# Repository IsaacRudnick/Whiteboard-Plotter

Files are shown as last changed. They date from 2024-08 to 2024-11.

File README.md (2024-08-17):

# VectorPlotter

:pushpin: If the system is set up and you just want to have it draw something, follow [these steps](/documentation/DrawSomething.md).

TODO: Picture of system on whiteboard

## Overview

This repository has everything necessary to assemble your own robot capable of plotting of SVG files on a whiteboard (or other surface). The existing code automatically handles outlining, scaling, and positioning of any SVG file along with commanding the robot to draw the image.

## Hardware

The VectorPlotter robot is built using an Arduino to handle implementation of the abstracted commands sent by the Python script. The robot is controlled by two stepper motors, one at each upper corner of the canvas. The pen is attached to a 3D-printed pen-holder assembly which uses a servo to raise and lower the pen, allowing noncontinuous lines to be drawn.

See the [Hardware Guide](/documentation/HardwareGuide.md) for a list of all necessary components and assembly instructions.

## Software

The VectorPlotter software is split into two parts: the Arduino code and the Python code. The Arduino code is responsible for interfacing with the hardware and executing the commands sent by the Python code. The Python code is responsible for reading the SVG file, scaling and positioning it on the canvas, and sending the commands to the Arduino to draw the image.

See the [Software Setup Guide](/documentation/SoftwareSetup.md) for a list of all necessary software and setup instructions.

## Usage

See the [How to Use](/documentation/DrawSomething.md) for instructions on how to use the software once everything is set up.

## Troubleshooting

See the [Troubleshooting Guide](/documentation/Troubleshooting.md) for common issues and solutions.

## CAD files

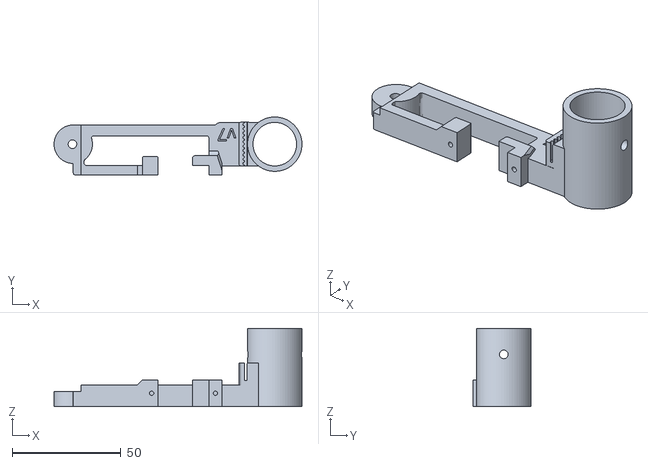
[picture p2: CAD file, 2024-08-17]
prints/VP_Pen_Holder.stl
113.9 x 26.7 x 36.0

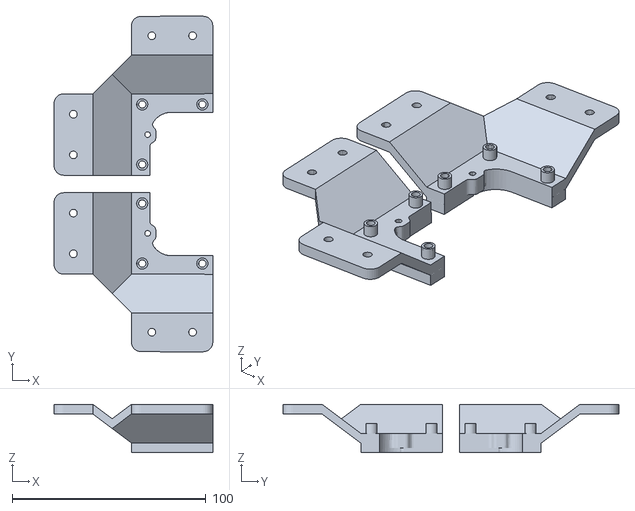
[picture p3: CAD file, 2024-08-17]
prints/VP_Bracket.stl
82.0 x 173.1 x 25.0

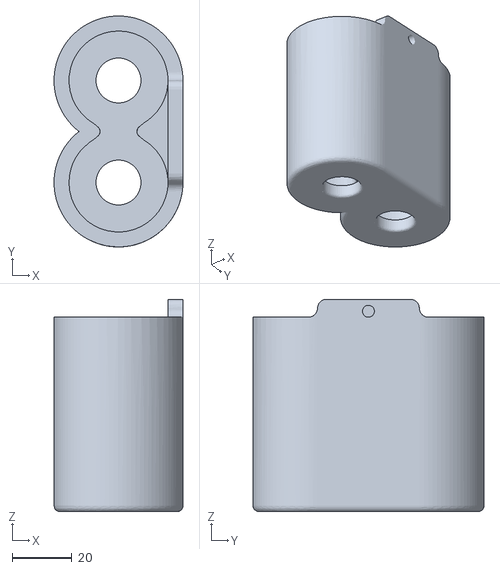
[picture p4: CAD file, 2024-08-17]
prints/VP_WeightHolder.stl
43.1 x 77.2 x 71.0

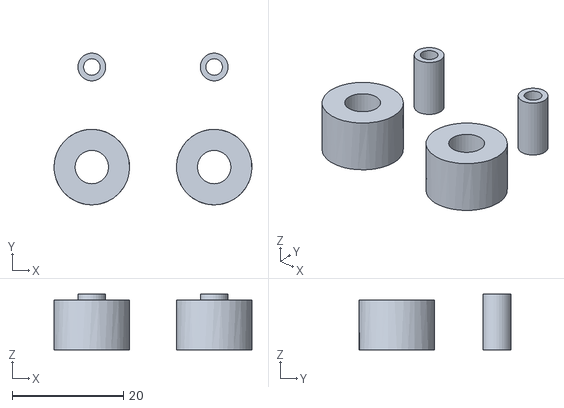
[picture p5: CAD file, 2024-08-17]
prints/VP_Sleeve_Spinner.stl
35.6 x 27.3 x 10.0

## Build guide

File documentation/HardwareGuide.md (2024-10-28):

# Hardware Requirements

## Items Needed

| Quantity | Name / Link |
| --- | --- |
| 1 | [Arduino Board](https://www.amazon.com/dp/B01EWOE0UU) with USB-B cable |
| 2 | [Stepper Motor Driver](https://www.amazon.com/dp/B075R88FMN) |
| 1 | [SG90 Micro Servo](https://www.amazon.com/dp/B07MLR1498) |
| 2 | [NEMA 17 Stepper Motors](https://www.amazon.com/dp/B0B38GHRH8) |
| 1 | [approx. 12V/1.5A DC Power Supply](https://www.amazon.com/dp/B0D2KNBHKG)  |
| 2 | [5mm Bore GT2 Pulley for 10mm Belt](https://www.amazon.com/dp/B09X18H75P) |
| 1 | [10mm 2GT Belt](https://www.amazon.com/dp/B0BYVC7K7J) |

> Note that only 2 pulleys are needed, but the link is for a pack of 5, so you only need to buy one pack.

There are also some misc. requirements which will depend on the specifics of your build. These include:

- Whiteboard, wall, etc. to plot on
- Whiteboard Marker, Sharpie, etc. to draw with
- Various Arduino Jumper Wires
- Some M3/M4 screws, washers, and nuts. [This kit](https://www.amazon.com/dp/B0CS67BLQJ) has all of the items needed:
  - 6 M3\*20 screws for attaching stepper motors to brackets
  - 2 M3\*16 screws and
  - 2 M3 washers for installing the bracket sleeve and spinner
  - 8 M4 screws for attaching brackets to whiteboard. Read note\*
  - 1 M4 screw and
  - 1 M4 nut for attaching/clamping the drawing implement to the pen holder
- 2 D-cell batteries for the weight holder. You may modify the weight holder for whatever weight you have (e.g., loose screws, nuts, etc.).
- A computer that can connect to the Arduino board. Consider a Raspberry Pi or an old laptop. It will need to stay connected for the duration of the drawing.

> \*Note: You may need to use different screws depending on the material of your whiteboard. I've found wood screws often work better than machine screws.

Finally, all prints in the [prints](/prints/) directory are required to build the robot.

| Name | Notes |
| --- | --- |
| VP_Bracket | Print with supports |
| VP_Pen_Holder | _None_ |
| VP_Sleeve_Spinner | Print with high infill and precision |
| VP_WeightHolder | _None_ |

# Hardware Setup

## Section 1: Wiring

The wiring setup is relatively simple. The following diagram shows how to connect the stepper motors, servo, and power supply to the Arduino board.
Wiring Diagram:

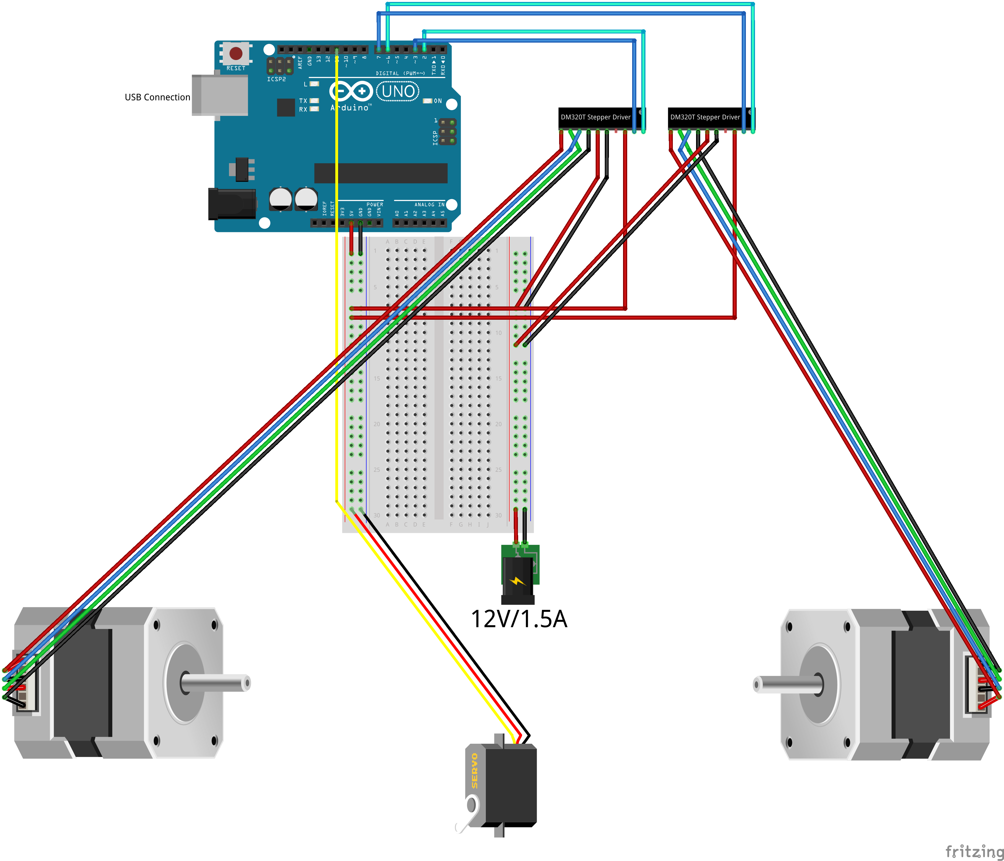
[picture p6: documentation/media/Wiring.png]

Example:

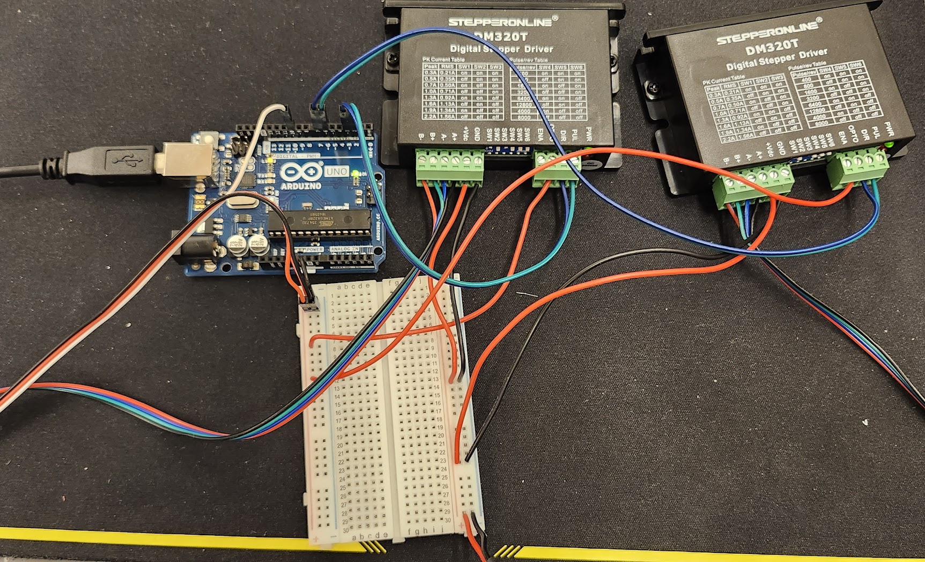
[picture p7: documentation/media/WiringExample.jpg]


## Section 2: Whiteboard

### Pen Holder Assembly

1. Install the SG90 Servo into the VP_Pen_Holder as shown below.

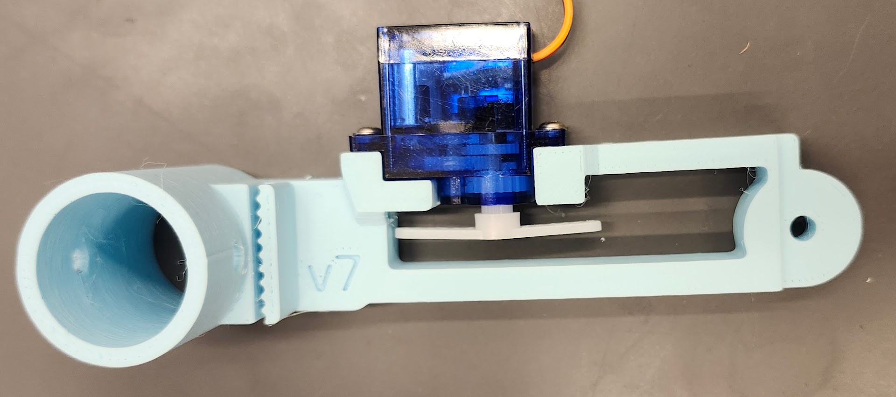
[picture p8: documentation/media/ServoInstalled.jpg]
   

1. Insert the midpoint of the belt into the VP_Pen_Holder
1. Place an M4 nut inside of the VP_Pen_Holder on the side closer to the servo.
1. Screw the M4 screw above the belt, through the VP_Pen_Holder, into the nut.

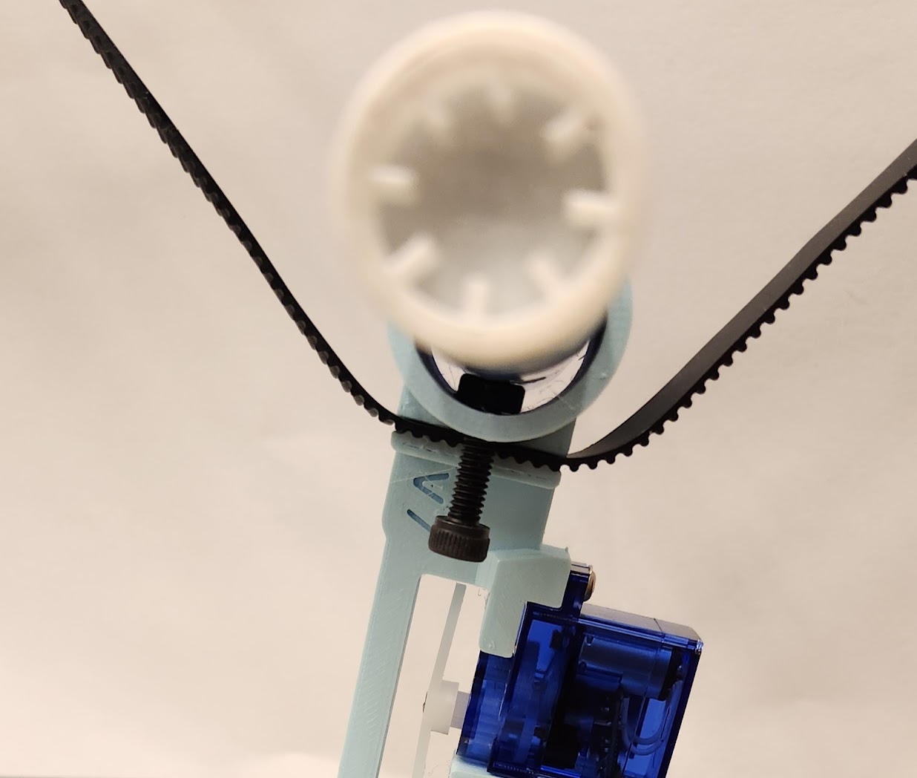
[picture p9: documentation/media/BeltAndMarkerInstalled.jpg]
   

1. Place two D-cell batteries into the VP_WeightHolder.
1. Screw an M4 screw through the VP_Pen_Holder and the VP_WeightHolder. The two should be firmly attached with no pivoting about the screw. Ensure the VP_WeightHolder is pressed flush against the VP_Pen_Holder.

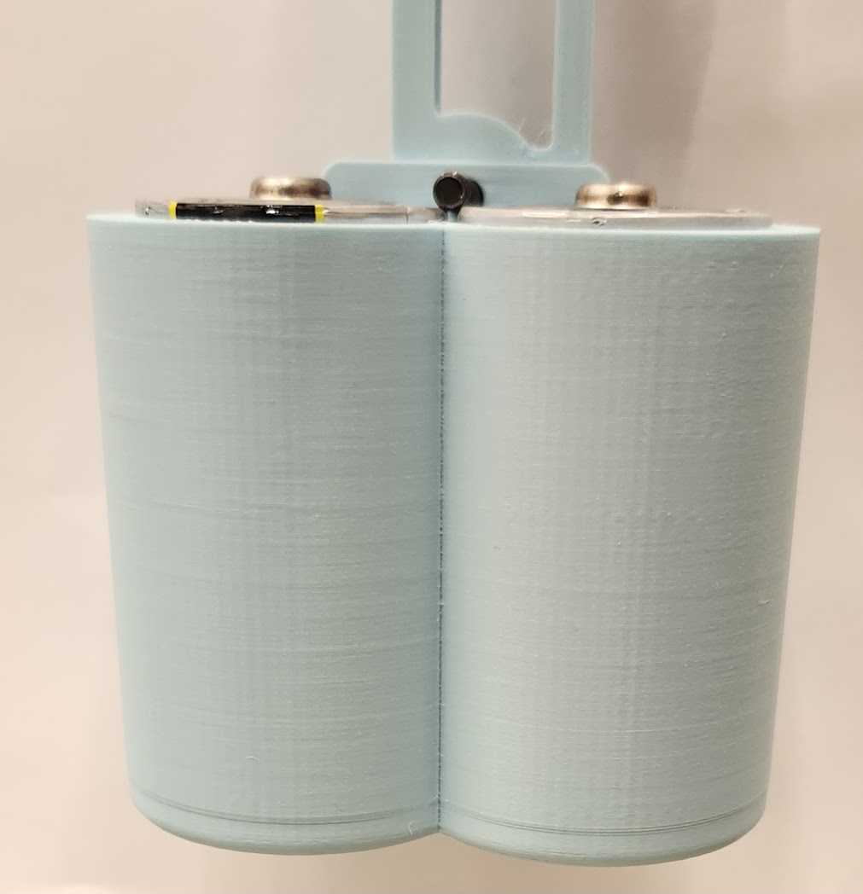
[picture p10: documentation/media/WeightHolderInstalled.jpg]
   

### Bracket Assembly

These steps will be repeated for both the left and right brackets. The pictures shown are for the right bracket, but the left bracket is a mirror image.

1. Screw an M3\*16 screw into one of the VP_Sleeve_Spinner print's smaller tubes (the "sleeve"). Place an M3 washer on the screw before screwing it in.
1. Insert the sleeve/washer/screw assembly into the larger VP_Sleeve_Spinner tube (the "spinner"). In this guide, for visibility,

- the sleeve is orange,
- the spinner is light blue, and
- the bracket is dark blue.

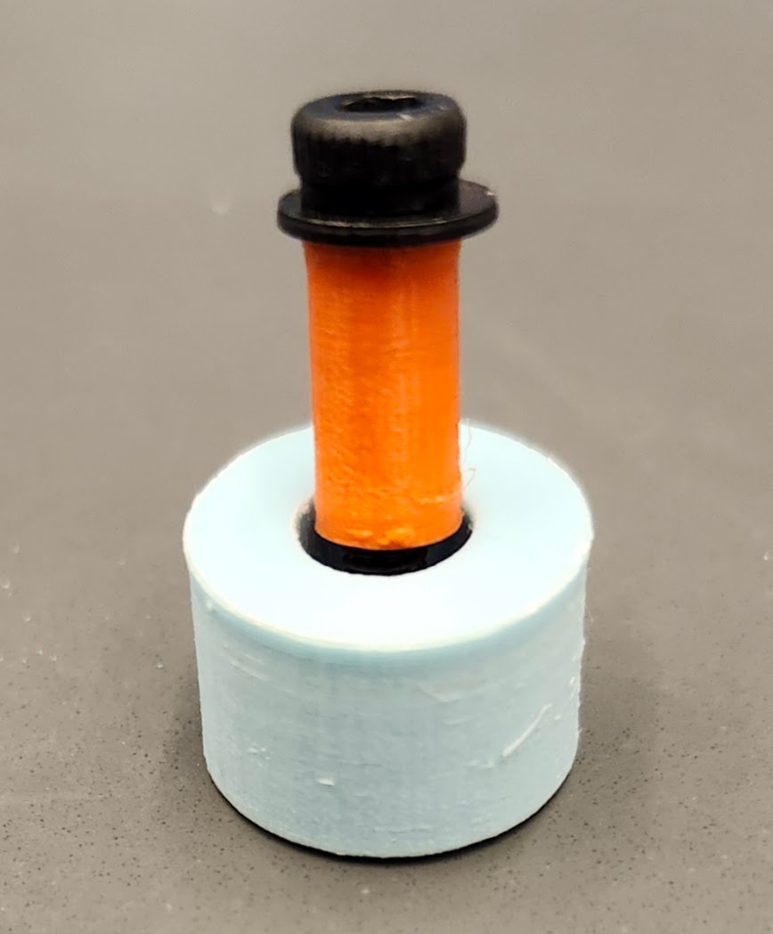
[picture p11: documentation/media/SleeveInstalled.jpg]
  

1. Screw the sleeve assembly (with the spinner around it) into the bracket as shown below.

   > The spinner should be loose and freely spin. It is ok if it wiggles when shaken.

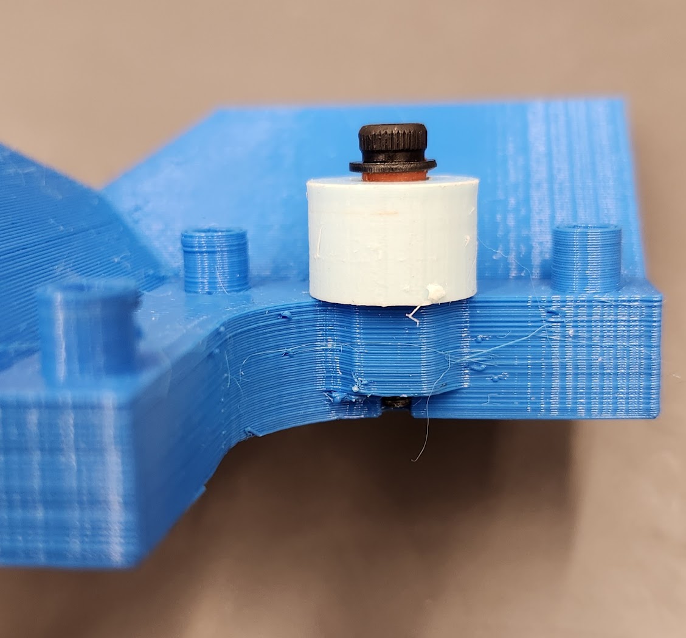
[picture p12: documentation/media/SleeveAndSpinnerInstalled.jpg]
   

1. Attach a pulleys to the stepper motor, ensuring the flat edge of the stepper motor shaft has a set screw pressing against it, as shown in the below example. Firmly tighten the set screws.

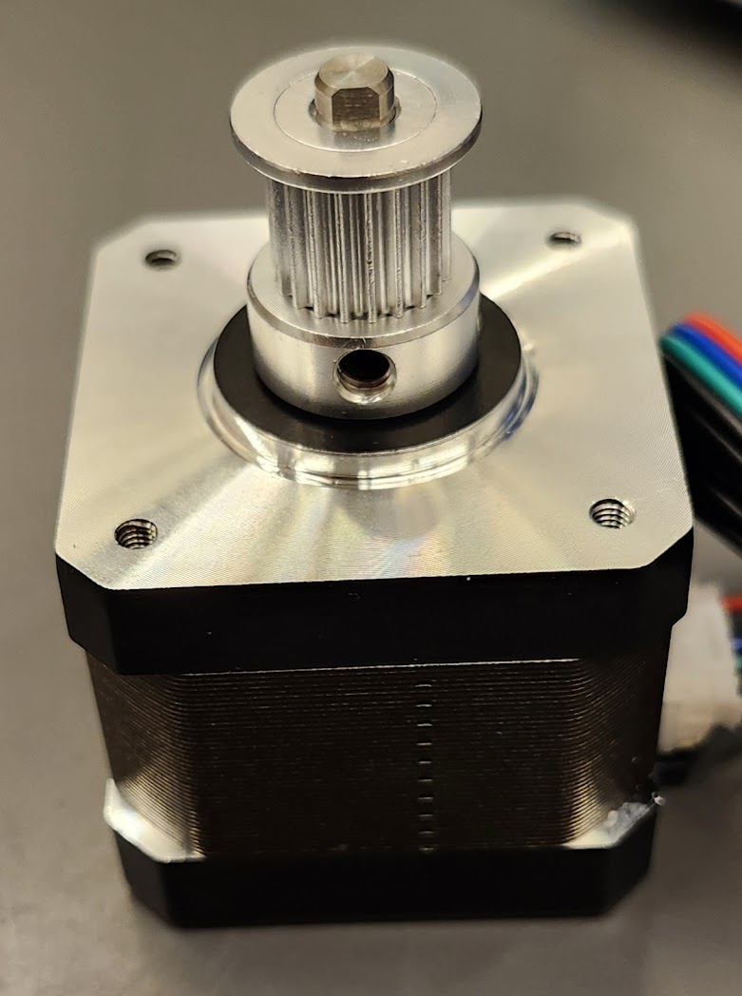
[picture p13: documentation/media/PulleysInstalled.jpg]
   

1. Attach the stepper motor to the VP_Bracket using M3\*20 screws. It is recommended to attach the stepper motor such that the wires are on one of the sides that will be facing away from the whiteboard. In the below image, those are the sides facing away from the camera.

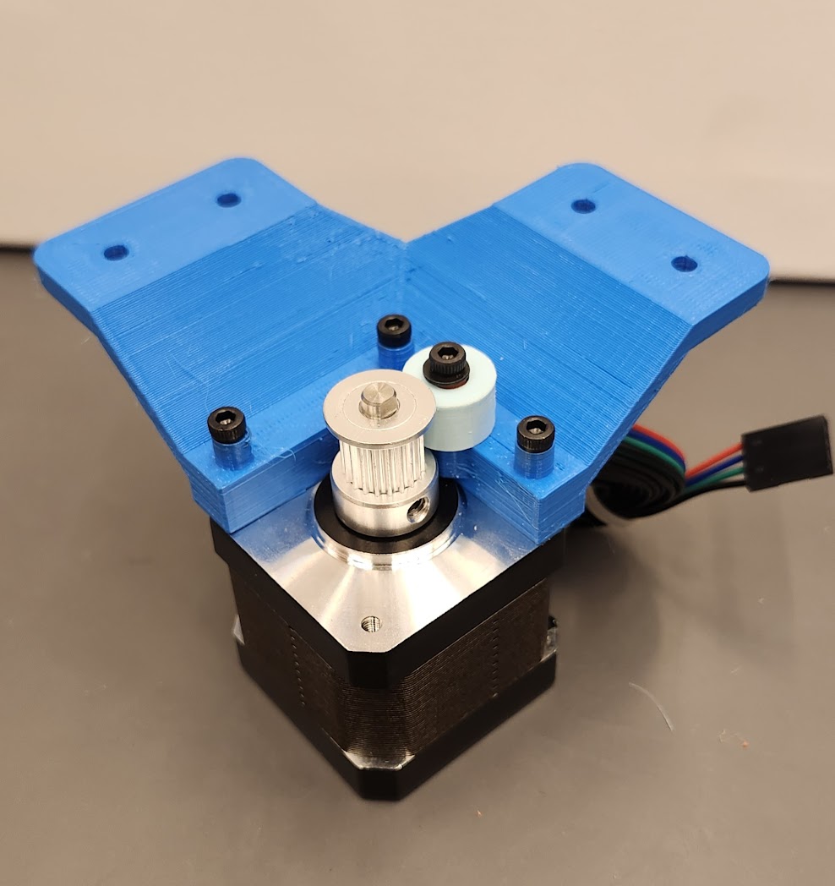
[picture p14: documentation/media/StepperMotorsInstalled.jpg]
   

1. By hand, rotate the belt into the pulley. Depower the steppers to facilitate this.
1. Attach the VP_Bracket to the whiteboard using M4 screws. On each bracket, the sleeve/spinner side should be the highest when installed (this is how to differentiate the left vs. right bracket).
   > It is recommended to drill holes in the whiteboard before screwing in the screws. You can use the bracket as a location template. Pre-drilling will help prevent the whiteboard from cracking.

This is what the top right corner of the whiteboard should look like when everything is installed (stepper wires not shown):

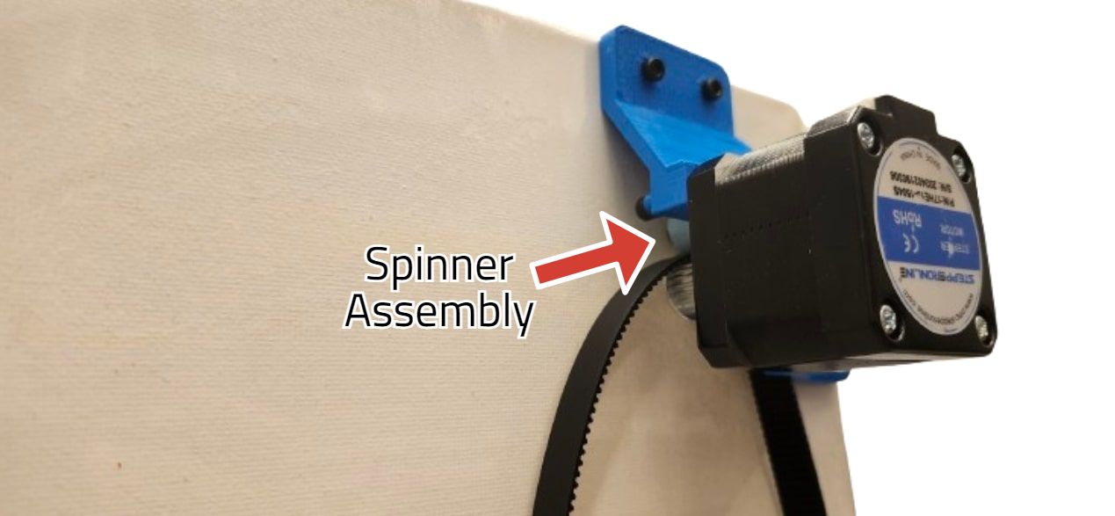
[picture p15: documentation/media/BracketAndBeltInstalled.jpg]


> Note the location of the spinner assembly, which is pointed at with a red arrow; it should be on the TOP of the belt, not to the side.

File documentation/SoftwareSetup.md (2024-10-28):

# Software Setup

This guide will walk you through the initial setup of the software, including dependencies and configuration.

## Install Dependencies

### PlatformIO

This project uses PlatformIO to manage dependencies and compile the code for the arduino. To install PlatformIO, follow the instructions on the [PlatformIO website](https://platformio.org/install/cli). You only need to upload the code to the Arduino once, so you can uninstall PlatformIO after the initial setup if you wish.

The PlatformIO project is located in the [arduino](/arduino/) directory. To upload the code to the Arduino,

1. Connect the Arduino to your computer via USB.
1. Install the PlatformIO extension in VSCode.
1. Open VSCode in the [arduino](/arduino/) directory.
1. Press `Ctrl+Alt+U` to upload the code to the Arduino.

Take note of the output from the upload process. If uploaded successfully, there should be a section that looks like this:

```
Looking for upload port...
Auto-detected: COM13
```

The port (COM13) will be used later.

### Python Setup

This project was tested with and works with Python 3.11.9. Other versions _should_ work but are untested.

Install all dependencies by running the following command in the root directory of the project:

```bash
pip install -r requirements.txt
```

## Set User Constants

The software has two constants files. The first is [constants.py](/constants.py), which contains the predefined constants for the software. The second is [user_setup.py](/user_setup.py), which you will need to set up.

`INPUT_IMG_FILE_PATH` - You will change this every time you want to draw a new image. This is the path to the SVG file you want to draw. The SVG file should be in the `user/SVGs/` directory, but this is not necessary.

`START_FROM_POINT` - This variable will be used if you want to draw a subset of an SVG. If, for some reason, the previous drawing was interrupted, you can set this variable to the point you want to start from. The default value is 0, which means the drawing will start from the beginning of the SVG. To see the point the last drawing was interrupted at, check the progress.txt file.

`MAX_CM_BETWEEN_POINTS` - used when interpolating points. Higher values will result in fewer points and faster drawing, but the drawing will be less accurate. Lower values will result in more points and slower drawing, but the drawing will be more accurate. The recommended value range is (0, 2]

`ARDUINO_USB_PORT` - The port that the Arduino is connected to. This is the port that was outputted when the code was uploaded to the Arduino. On Windows, it will look something like `COM13`. On Linux, it will look something like `/dev/ttyACM0`. If you want to find this port without uploading the arduino again, you can run the [lisb_usb_ports.py](/list_usb_ports.py) file. The port connected to the arduino will likely have "Serial" or "Arduino" in its name.

`SHOW_PREVIEW` - Whether or not to show a preview on the screen before drawing the SVG. Useful for confirming that the SVG is being placed and scaled correctly.

`TURTLE_PENSIZE` - the width of the pen in pixels. Only affects preview, not actual drawing.

`BACKGROUND_IMG_FILE_PATH` - The path to the image file that will be used as the background. This is optional. If you don't want a background image, set this to `None`.

More about the below values can be found in the [Canvas Explained](#canvas-explained) section.
`CANVAS_WIDTH` - The width in cm of the canvas.  
`CANVAS_HEIGHT` - The height in cm of the canvas.
`TOP_PADDING` - The distance in cm between the top of the canvas and the drawable area.
`LEFT_PADDING` - The distance in cm between the left side of the canvas and the drawable area.
`RIGHT_PADDING` - The distance in cm between the right side of the canvas and the drawable area.
`BOTTOM_PADDING` - The distance in cm between the bottom of the canvas and the drawable area.

### Canvas Explained

The "canvas" is a rectangular area defined by the distance between the stepper motor shafts and the distance from the stepper motor's shaft to the bottom of the board. The "frame" is the user-defined area within the canvas where the user permits the pen to draw.

The following term

| Term | Definition |
| --- | --- |
| Canvas Width | The distance in cm between the center of each stepper |
| Canvas Height  | The distance in cm between the center of the stepper and the bottom of the board |
| Frame | The drawable rectangular subarea of the canvas. Defined by the padding |
| Left Padding | The user-defined distance between the left side of the canvas and the drtawable area |
| Right Padding  | The user-defined distance between the right side of the canvas and the drawable area |
| Top Padding | The user-defined distance between the top of the canvas and the drawable area |
| Bottom Padding | The user-defined distance between the bottom of the canvas and the drawable area |

The below image illustrates these terms. In this image, the white rectangle represents the frame, which is the only area where the pen is allowed to draw.
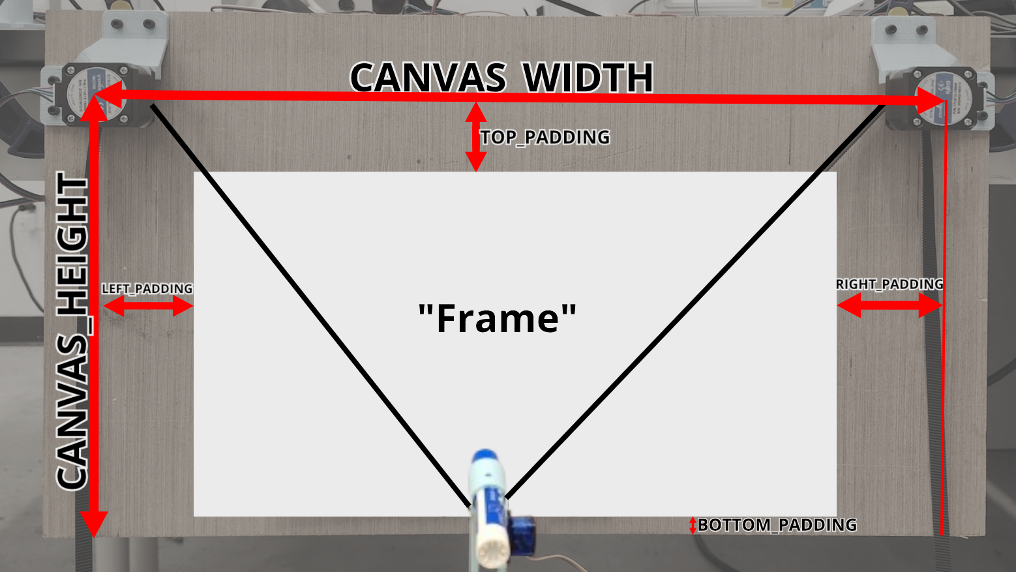
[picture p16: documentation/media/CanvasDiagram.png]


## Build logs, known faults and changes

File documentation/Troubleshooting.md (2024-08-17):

# Troubleshooting

## Table of Contents

## My motors or servo are not moving

## My motors are moving in the wrong direction

## My pen is not lifting or lowering properly

## The image curves upwards or downwards

## The image/preview don't look like my input SVG

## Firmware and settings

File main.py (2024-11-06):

from dataclasses import dataclass
from math import sqrt
import os
import time
from svgoutline import svg_to_outlines
import turtle
import constants
import user_setup as user_settings
import xml.etree.ElementTree as ET
from progress.bar import ChargingBar
import cv2
import pycomponents.ArduinoInterface as ArduinoInterface
from pycomponents.Stepper import StepperDirection as StepperDirection
from pycomponents.Servo import ServoConnectionType, ServoActuationType, ServoInverted 

# =========================================== WARNINGS =========================================== #
# Make sure user isn't accidentally starting from a point other than 0
if user_settings.START_FROM_POINT > 0:
    warning = f"NOTE: Starting from point {user_settings.START_FROM_POINT}. Press Enter to continue."
    input(warning)

# Minimum recommended padding values
min_lp = 5
min_rp = 5
min_tp = 10
min_bp = 5

# Check the padding values and warn the user if they are below the recommended minimums
lp_warning = user_settings.LEFT_PADDING < min_lp
rp_warning = user_settings.RIGHT_PADDING < min_rp
tp_warning = user_settings.TOP_PADDING < min_tp
bp_warning = user_settings.BOTTOM_PADDING < min_bp

if lp_warning or rp_warning or tp_warning or bp_warning:
    print(
        f"WARNING: Padding values are " +
        f"left: {user_settings.LEFT_PADDING}, " +
        f"right: {user_settings.RIGHT_PADDING}, " +
        f"top: {user_settings.TOP_PADDING}, " +
        f"bottom: {user_settings.BOTTOM_PADDING}.\n " +
        "Recommended minimum values are " +
        f"{min_lp}, {min_rp}, {min_tp}, {min_bp}. "
        "Make sure the pen holder fits within the canvas.")
    input("Press Enter to acknowledge.")

# ===================================== Classes and Instances ==================================== #

# Create the steppers and servo that control the physical plotter
TopLeftStepper =  ArduinoInterface.Stepper(0, StepperDirection.NORMAL)
TopRightStepper = ArduinoInterface.Stepper(1, StepperDirection.INVERTED)
MarkerToggleServo = ArduinoInterface.Servo(0,
                                           ServoConnectionType.PWM,
                                           ServoActuationType.POSITION,
                                           (500, 1500),
                                           (0, 180),
                                           ServoInverted.NORMAL)
SteppersFinishedSensor = ArduinoInterface.Sensor(0)
Arduino = ArduinoInterface.Arduino(user_settings.ARDUINO_USB_PORT,
                                   [MarkerToggleServo],
                                   [TopLeftStepper, TopRightStepper],
                                   [SteppersFinishedSensor])


@dataclass
class PointInstruction:
    """Represents a point in the drawing with instructions for the motors and pen.
    x_cm and y_cm are the coordinates of the point in cm, where the bottom left of the canvas is (0,0).
    motor_left_position and motor_right_position are the number of steps each motor needs to take to reach that point.
    pen_down_after is a boolean value that determines whether the pen should be down after reaching that point.
    """
    x_cm: float
    y_cm: float
    # Map the x and y cm to the position of each motor (in steps) to reach that point.
    # Note, steps are relative to start, not current position.
    motor_left_position: int
    motor_right_position: int
    # Put the pen down after this point or not
    pen_down_after: bool


class PenController:
    def __init__(self, ArdI: ArduinoInterface.Arduino):
        self.ArdI = ArdI

        self.pen_down = True  # Initial pen state
        self.prev_instruction = None

    def raise_pen(self):
        if self.pen_down:
            self.ArdI.set_servo(MarkerToggleServo, constants.PEN_UP_SERVO_ANGLE)
            # Wait for the steppers to finish moving before continuing
            time.sleep(0.5)
            self.pen_down = False

    def lower_pen(self):
        if not self.pen_down:
            self.ArdI.set_servo(MarkerToggleServo, constants.PEN_DOWN_SERVO_ANGLE)
            # Wait for the steppers to finish moving before continuing
            time.sleep(0.5)
            self.pen_down = True
            
    def done_moving(self):
        return self.ArdI.poll_sensor(SteppersFinishedSensor)

    def follow_instruction(self, instruction: PointInstruction):
        # Move the motors to the correct position
        self.ArdI.set_stepper(TopLeftStepper, instruction.motor_left_position)
        self.ArdI.set_stepper(TopRightStepper, instruction.motor_right_position)

        # Wait for the steppers to finish moving before continuing
        while not self.done_moving():
            print("Debug: Waiting for steppers to finish moving.")
            time.sleep(0.1)

        if instruction.pen_down_after:
            self.lower_pen()
        else:
            self.raise_pen()

        # Update the previous instruction
        self.prev_instruction = instruction


# This is how we will control moving the pen across the board and raising/lowering it (on/off the surface)
Pen = PenController(Arduino)

# ======================================= PRIMARY FUNCTIONS ====================================== #


def add_strokes_to_svg(input_file: str, output_file: str):
    """Add stroke and stroke-width attributes to all elements in an SVG file.
    This is necessary for the svgoutline library to work properly.

    Args:
        input_file (str): The path to the input SVG file.
        output_file (str): The path to the output SVG file.
    """
    # Parse the SVG file
    tree = ET.parse(input_file)
    root = tree.getroot()

    # Iterate over all elements in the SVG
    for elem in root.iter():
        # Add stroke and stroke-width attributes to each element
        # The color and width are arbitrary as far as this program is concerned. All that matters is that they are there.
        elem.set('stroke', 'red')
        elem.set('stroke-width', '2')

    # Write the updated SVG to a new file
    tree.write(output_file)


def svg_to_instructions(svg_path: str):
    """Generate a list of PointInstructions from an SVG file.

    Args:
        svg_path (str): The path to the SVG file that will be converted to instructions.
    """

    # ====================================== GET STARTING POINTS ===================================== #

    frame_width = user_settings.CANVAS_WIDTH - user_settings.LEFT_PADDING - user_settings.RIGHT_PADDING
    frame_height = user_settings.CANVAS_HEIGHT - user_settings.TOP_PADDING - user_settings.BOTTOM_PADDING

    # Get raw points. These will later be scaled to the canvas size, but may have any range of values right now.
    tree = ET.parse(svg_path)
    root = tree.getroot()
    outlines = svg_to_outlines(root)
    # List of lists of points. Each sublist is a disconnected section of the drawing.
    raw_sections = [line[2] for line in outlines]

    raw_all_points = [point for section in raw_sections for point in section]

    # Determine the minimum and maximum x and y values of the drawing
    # These will be used to scale the drawing to the canvas size
    min_x = min([point[0] for point in raw_all_points])
    max_x = max([point[0] for point in raw_all_points])
    min_y = min([point[1] for point in raw_all_points])
    max_y = max([point[1] for point in raw_all_points])

    # ============================================ SCALING =========================================== #
    # Scale all points to fit in the frame

    # Calculate the scale factor to fit the drawing to the canvas
    x_scale_factor = frame_width / (max_x - min_x)
    y_scale_factor = frame_height / (max_y - min_y)

    # Maintain aspect ratio by using the smaller scale factor
    scale_factor = min(x_scale_factor, y_scale_factor)

    # Calculate the center offset to keep the drawing centered
    x_center_offset = (frame_width - (max_x - min_x) * scale_factor) / 2
    y_center_offset = (frame_height - (max_y - min_y) * scale_factor) / 2

    def scale_raw_xy(x, y):
        """Take in a raw x and y value and scale it to the canvas size. Only used in svg_to_instructions."""
        scaled_x = (x - min_x) * scale_factor + user_settings.LEFT_PADDING + x_center_offset
        scaled_y = (y - min_y) * scale_factor + y_center_offset
        scaled_y = user_settings.CANVAS_HEIGHT - user_settings.TOP_PADDING - scaled_y
        return scaled_x, scaled_y

    sections = []

    for raw_section in raw_sections:
        section = [scale_raw_xy(x, y) for x, y in raw_section]
        sections.append(section)

    # ====================================== INTERMEDIATE POINTS ===================================== #
    # Add intermediate points in the drawing. Necessary to avoid arcs when drawing straight lines.

    def add_intermediate_points(section):
        """Add intermediate points to the sections to smooth out the drawing.

        Args:
            section (list): List of points [(x1, y1), (x2, y2), ...]

        Returns:
            list: New section with intermediate points.
        """
        new_section = []
        for i in range(len(section) - 1):
            x1, y1 = section[i]
            x2, y2 = section[i + 1]
            new_section.append((x1, y1))
            distance = sqrt((x2 - x1) ** 2 + (y2 - y1) ** 2)
            num_points = int(distance // user_settings.MAX_CM_BETWEEN_POINTS)
            for j in range(1, num_points + 1):
                new_x = x1 + j * (x2 - x1) / (num_points + 1)
                new_y = y1 + j * (y2 - y1) / (num_points + 1)
                new_section.append((new_x, new_y))
        new_section.append(section[-1])
        return new_section

    interpolated_sections = [add_intermediate_points(section) for section in sections]

    # ======================================== MOTOR DISTANCES ======================================= #

    def xy_to_motor_position(x, y):
        steps_per_cm = constants.STEPS_PER_REVOLUTION * constants.REVOLUTIONS_PER_CM
        cm_from_top = user_settings.CANVAS_HEIGHT - y - constants.PEN_VERTICAL_OFFSET
        cm_from_right = user_settings.CANVAS_WIDTH - x + constants.PEN_HOLDER_WIDTH
        cm_from_left = x + constants.PEN_HOLDER_WIDTH
        top_left_motor_position = steps_per_cm * sqrt(cm_from_top ** 2 + cm_from_left ** 2)
        top_right_motor_position = steps_per_cm * sqrt(cm_from_top ** 2 + cm_from_right ** 2)
        return top_left_motor_position, top_right_motor_position

    instructions = []

    for section in interpolated_sections:
        for x, y in section:
            motor_left_position, motor_right_position = xy_to_motor_position(x, y)
            instructions.append(PointInstruction(x, y, motor_left_position, motor_right_position, True))

        # At the end of each section, lift the pen up
        instructions[-1].pen_down_after = False

    return instructions


def prep_background(input: str, output: str, width: int, height: int):
    """Helper function for draw().
    Resizes the input image that will be the background of the drawing.
    Also adds a rectangle to the turtle screen to represent the area inside the canvas padding.

    Args:
        input (str): The path to the input image.
        output (str): The path to the output image.
        width (int): The desired width of the image in pixels.
        height (int): The desired height of the image in pixels.
    """
    # Used to draw the rectangle representing the canvas padding
    width_scale = width / user_settings.CANVAS_WIDTH
    height_scale = height / user_settings.CANVAS_HEIGHT

    line_thickness = 2

    # cv2 rectangle origin is top left. Positive x is right, positive y is down
    # The +- 10 offsets adjust for some small rounding issues. It will ONLY affect the preview, not the actual drawing.
    x0 = int(user_settings.LEFT_PADDING * width_scale) - line_thickness * 2 - 10
    y0 = int((user_settings.TOP_PADDING) * height_scale) + line_thickness * 2 + 10

    x1 = int((user_settings.CANVAS_WIDTH - user_settings.RIGHT_PADDING) * width_scale) + line_thickness * 2 - 10
    y1 = int((user_settings.CANVAS_HEIGHT - user_settings.BOTTOM_PADDING) * height_scale) - line_thickness * 2 + 10

    img = cv2.imread(input)
    resized = cv2.resize(img, (width, height))
    cv2.rectangle(resized,
                  (x0, y0),
                  (x1, y1),
                  (0, 0, 0),
                  line_thickness,
                  lineType=cv2.LINE_AA)
    cv2.imwrite(output, resized)


def draw(instructions: list[PointInstruction], only_preview=False):
    """Draw the given instructions on the canvas. Show a digital preview of the drawing as well

    Args:
        instructions (list[PointInstruction]): The list of instructions to draw.
        only_preview (bool, optional): Whether to only show a preview of the drawing. Defaults to False.
    """

    # ================================ TURTLE, CANVAS, AND BACKGROUND ================================ #
    screen = turtle.Screen()

    # Get starting screen width and height of the window
    screen_width, screen_height = screen.window_width(), screen.window_height()
    # Scale the window / screen to the canvas size, maintaining aspect ratio
    if screen_width / user_settings.CANVAS_WIDTH < screen_height / user_settings.CANVAS_HEIGHT:
        screen_height = int(screen_width * user_settings.CANVAS_HEIGHT / user_settings.CANVAS_WIDTH)
    else:
        screen_width = int(screen_height * user_settings.CANVAS_WIDTH / user_settings.CANVAS_HEIGHT)
    screen.setup(width=screen_width, height=screen_height)

    # Configure how coordinates are interpreted. (0,0) will be bottom left, (CANVAS_WIDTH, CANVAS_HEIGHT) will be top right
    screen.setworldcoordinates(0, 0, user_settings.CANVAS_WIDTH, user_settings.CANVAS_HEIGHT)

    turtle_canvas = screen.getcanvas()

    # Add the background image if it exists
    if user_settings.BACKGROUND_IMG_FILE_PATH:
        prep_background(user_settings.BACKGROUND_IMG_FILE_PATH,
                        "temp/ResizedBackground.png",
                        screen_width, screen_height)
        # Set the background image to be the resized image and make sure its aligned properly
        screen.bgpic("temp/ResizedBackground.png")
        turtle_canvas.itemconfig(screen._bgpic, anchor="sw")

    root = turtle_canvas.winfo_toplevel()
    root.resizable(False, False)
    root.title("Drawing Preview")

    # Bug-fixing line that allows us to recreate the turtle window if this function is called multiple times.
    turtle.TurtleScreen._RUNNING = True

    t = turtle.Turtle()
    t.pensize(user_settings.TURTLE_PENSIZE)
    t.color("green") if only_preview else t.color("blue")
    t.setheading(90)  # Point the turtle up

    t.penup()

    # Progress bar to show how many points have been drawn. Will be shown in the console.
    bar = ChargingBar('Drawing', max=len(instructions))

    # ====================================== DRAWING THE POINTS ====================================== #
    for i, instruction in enumerate(instructions):
        # Skip to the starting point
        if i < user_settings.START_FROM_POINT:
            bar.next()
            continue

        t.goto(instruction.x_cm, instruction.y_cm)
        t.pendown() if instruction.pen_down_after else t.penup()

        # If we are actually drawing and not just previewing, follow the instructions
        if not only_preview:
            Pen.follow_instruction(instruction)
            save_progress(i)

        bar.next()

    print("\n")

    # If the actual drawing is complete, remove the progress file
    if not only_preview:
        os.remove("progress.txt")

    print("Click window to exit.")
    turtle.exitonclick()
    print("Drawing complete.")


def save_progress(total_points_drawn: int):
    try:  # Save progress in case of interruption
        with open("progress.txt", "w") as f:
            f.write(str(total_points_drawn))
    except PermissionError:
        print("Could not save progress. Make sure progress.txt is not open.")


if __name__ == "__main__":
    # Always raise the pen to start. This is to prevent the pen from drawing when it shouldn't.
    print("Raising pen...")
    Pen.raise_pen()

    print("Preprocessing SVG file...")
    add_strokes_to_svg(user_settings.INPUT_IMG_FILE_PATH, 'temp/output.svg')
    print("Converting SVG to instructions...")
    instructions = svg_to_instructions('temp/output.svg')

    if user_settings.SHOW_PREVIEW:
        print("Showing preview...")
        draw(instructions, only_preview=True)
        input("Press Enter to confirm preview and start drawing.")

    print("Drawing...")
    draw(instructions)

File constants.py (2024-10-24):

# ====================================== PRELOADED CONSTANTS ===================================== #
# Distance between belt ends in the holder.
PEN_HOLDER_WIDTH = 2.5  # cm
# How high above the belt the pen is.
PEN_VERTICAL_OFFSET = 2  # cm

# ====================================== STEPPERS AND SERVOS ===================================== #
STEPS_PER_REVOLUTION = 400  # Turning the motor 400 steps = one revolution
REVOLUTIONS_PER_CM = 0.25  # From testing, Driving the belt 1 cm requires 0.25 revolutions.

PEN_DOWN_SERVO_ANGLE = 30
PEN_UP_SERVO_ANGLE = -90

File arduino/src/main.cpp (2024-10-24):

#include <Wire.h>
#include <SPI.h>
#include <Adafruit_PWMServoDriver.h>
#include <AccelStepper.h>
#include "Steppers.h"
#include "Servos.h"
#include "Sensors.h"

// The absolute maximum microseconds for a servo pulse.
// This is a backup safety limit to avoid breaking servos.
#define MAX_SERVO_MICROS 3000
#define MIN_SERVO_MICROS 0
// Constants
#define SERVO_FREQ 50 // Analog servos run at ~50 Hz updates

// Initialize PWM servo driver
Adafruit_PWMServoDriver pwm = Adafruit_PWMServoDriver();

// Enumeration for command types
enum class CommandType : char
{
    ShieldServo = 's',
    Stepper = 't',
    Sensor = 'i',
    LooseServo = 'l',
    Unknown = 'X'
};

// Structure to represent a parsed command
struct Command
{
    CommandType type;
    int index;
    long value;   // For set commands
    bool isQuery; // True for query commands like 'i2?'

    Command() : type(CommandType::Unknown), index(-1), value(0), isQuery(false) {}
};

// Example commands:
// "s0=1500;" - Set shield servo 0 to 1500 microseconds
// "t0=100;" - Move stepper 0 to position 100
// "i2?;" - Query sensor 2
// "l1=2000;" - Set loose servo 1 to 2000 microseconds (of 50Hz PWM)
// "s2=1000;t1=200;i0?;" - Set shield servo 2 to 1000, move stepper 1 to 200, query sensor 0

// Function Prototypes
void runAllSteppers();
bool parseCommand(const String &input, Command &cmd);
void processCommands(const String &input);
void executeCommand(const Command &cmd);

void setup()
{
    // Initialize Serial communication
    Serial.begin(115200);
    Serial.setTimeout(100); // Set timeout for Serial.readString()
    Serial.println("Initializing...");

    // Initialize PWM servo driver
    pwm.begin();
    pwm.setOscillatorFrequency(27000000);
    pwm.setPWMFreq(SERVO_FREQ);

    // Initialize peripherals
    setupSteppers();
    setupServos();
    setupSensors();
}

void loop()
{
    // Check if data is available on Serial
    if (Serial.available())
    {
        String incomingData = Serial.readString();
        incomingData.trim(); // Remove leading and trailing whitespace

        // Serial.println(incomingData);

        if (incomingData.length() > 0)
        {
            processCommands(incomingData);
        }
    }

    // Continuously run steppers
    runAllSteppers();
}

/**
 * @brief Processes all commands in the input string separated by ';'
 * @param input String containing one or multiple commands
 */
void processCommands(const String &input)
{
    int start = 0;
    int end = input.indexOf(';');

    while (end != -1)
    {
        runAllSteppers(); // Ensure steppers are updated regularly

        String commandStr = input.substring(start, end);
        commandStr.trim(); // Clean up the command string

        if (commandStr.length() > 0)
        {
            Command cmd;
            if (parseCommand(commandStr, cmd))
            {
                executeCommand(cmd);
            }
        }

        start = end + 1;
        end = input.indexOf(';', start);
    }
}

/**
 * @brief Parses a single command string into a Command object
 * @param input The command string (e.g., "s0=1500" or "i2?")
 * @param cmd Reference to a Command object to populate
 * @return True if parsing is successful, else False
 */
bool parseCommand(const String &input, Command &cmd)
{
    if (input.length() < 2)
    {
        Serial.println("!Error: Command too short.");
        return false;
    }

    // Determine command type
    char typeChar = input.charAt(0);
    cmd.type = static_cast<CommandType>(typeChar);

    // Handle query commands (ending with '?')
    int queryPos = input.indexOf('?');
    if (queryPos != -1)
    {
        String indexStr = input.substring(1, queryPos);
        cmd.index = indexStr.toInt();
        cmd.isQuery = true;
        return true;
    }

    // Handle set commands (containing '=')
    int equalsPos = input.indexOf('=');
    if (equalsPos == -1)
    {
        Serial.println("!Error: Invalid command format. Missing '=' or '?'");
        return false;
    }

    String indexStr = input.substring(1, equalsPos);
    String valueStr = input.substring(equalsPos + 1);

    cmd.index = indexStr.toInt();
    cmd.value = valueStr.toInt();
    cmd.isQuery = false;

    return true;
}

/**
 * @brief Executes a parsed Command
 * @param cmd The Command to execute
 */
void executeCommand(const Command &cmd)
{
    switch (cmd.type)
    {
    case CommandType::ShieldServo:
        if (cmd.index >= 0 && cmd.index < 16)
        {
            int servoValue = constrain(cmd.value, 0, MAX_SERVO_MICROS);
            pwm.writeMicroseconds(cmd.index, servoValue);
        }
        else
        {
            Serial.println("!Error: Invalid shield servo index.");
        }
        break;

    case CommandType::Stepper:
        if (cmd.index >= 0 && cmd.index < steppersCount)
        {
            steppers[cmd.index].moveTo(cmd.value);
        }
        else
        {
            Serial.println("!Error: Invalid stepper index.");
        }
        break;

    case CommandType::Sensor:
        if (cmd.isQuery)
        {
            if (cmd.index >= 0 && cmd.index < sensorsCount)
            {
                int sensorValue = sensors[cmd.index]->read();
                // Format: "i{index}={value}"
                // Example: "i2=1000"
                Serial.print("i");
                Serial.print(cmd.index);
                Serial.print("=");
                Serial.println(sensorValue);
            }
            else
            {
                Serial.println("!{Error: Invalid sensor index.}");
            }
        }
        else
        {
            Serial.println("!{Error: Sensor command should be a query (e.g., 'i2?').}");
        }
        break;

    case CommandType::LooseServo:
        if (cmd.index >= 0 && cmd.index < looseServosCount)
        {
            int servoValue = constrain(cmd.value, 0, MAX_SERVO_MICROS);
            looseServos[cmd.index].writeMicroseconds(servoValue);
        }
        else
        {
            Serial.println("!{Error: Invalid loose servo index.}");
        }
        break;

    default:
        Serial.println("!{Error: Unknown command type.}");
        break;
    }
}

/**
 * @brief Runs all steppers that need stepping. Must be called as frequently as possible!
 */
void runAllSteppers()
{
    // static unsigned long lastStepTime = 0;
    // unsigned long currentTime = micros();
    // unsigned long timeElapsed = currentTime - lastStepTime;
    // lastStepTime = currentTime;

    // Optional: Debugging lag in stepper updates
    // if (timeElapsed > 500) {
    //     Serial.printf("Stepper update lag: %lu microseconds\n", timeElapsed);
    // }

    for (int i = 0; i < steppersCount; ++i)
    {
        steppers[i].run();
    }
}

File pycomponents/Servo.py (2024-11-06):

from enum import Enum
from pycomponents.utils import map, clamp


class ServoConnectionType(Enum):
    SHIELD = 's'
    LOOSE = 'l'


class ServoActuationType(Enum):
    POSITION = 'p'
    VELOCITY = 'v'


class ServoInverted(Enum):
    NORMAL = 1
    INVERTED = -1


class Servo:
    def __init__(self,
                 pin_or_index: int,
                 connection_type: ServoConnectionType,
                 actuation_type: ServoActuationType,
                 microsecond_range: tuple[int, int],
                 actuation_range: tuple[int, int],
                 inverted: ServoInverted):
        """Creates a servo object with the given parameters

        Args:
            pin_or_index (int): The index of the servo in the arduino Servos.h header file OR the pin the servo is connected to (if SHIELD)
            connection_type (ServoConnectionType): The connection type of the servo
            actuation_type (ServoActuationType): The actuation type of the servo
            microsecond_range (tuple[int, int]): The range of microsecond values that the servo can be set to. Format: (lower, upper)
            actuation_range (tuple[int, int]): The range of actuation values that the servo can be set to. Format: (lower, upper). Likely degrees or velocities.

        Raises: 
            ValueError: If the pin is greater than 15 and the connection type is SHIELD
            ValueError: If the microsecond ranges are not positive

        Example usage:
            ServoType(ServoConnectionType.SHIELD, ServoActuationType.POSITION, (1000, 2000), (0, 180), ServoInverted.NORMAL) 
            represents a servo that is connected to the shield, is position controlled, can be set to a range of 1000-2000 microseconds, and can be set to a range of 0-180 degrees.
            Degrees could alternatively be (-90, 90) for a servo that can only rotate 180 degrees. How you wish to set this will be up to you.
        """

        if pin_or_index > 15 and connection_type == ServoConnectionType.SHIELD:
            raise ValueError("Shield-connected servos' pins must be less than or equal to 15. ")

        if microsecond_range[0] < 0 or microsecond_range[1] < 0:
            raise ValueError("Microsecond ranges must be positive.")

        self.pin_or_index = pin_or_index
        self.connection_type = connection_type
        self.actuation_type = actuation_type
        self.microsecond_range = microsecond_range
        self.actuation_range = actuation_range
        self.inverted = inverted

        self.actuation_value = None

    def mark_actuation_value(self, value: int):
        """Updates the actuation value (degrees or velocity) of the servo.

        Args:
            value (int): The new actuation value of the servo
        """
        self.actuation_value = value

    def actuation_value_to_arduino_value(self, value: int) -> int:
        """Converts the actuation value to a microsecond value.

        Args:
            value (int): The actuation value to convert to microseconds

        Returns:
            int: The actuation value converted to microseconds
        """

        # Clamp the value to the actuation range to prevent out-of-range values
        value = clamp(self.actuation_range[0], value, self.actuation_range[1])

        # Map the value from the actuation range to the microsecond range
        in_min, in_max = self.actuation_range
        out_min, out_max = self.microsecond_range

        # If the servo is inverted, invert the value before mapping
        # When working with this code, remember that the servo's actuation range may not be equal about 0.
        # E.g. it could be -20 to 100 degrees.
        if self.inverted == ServoInverted.INVERTED:
            value = self.actuation_range[1] - value

        return int(map(value, in_min, in_max, out_min, out_max))

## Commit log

2024-08-17 Initial commit. Working prototype on practice surface.
    [VP_Bracket.stl, VP_Pen_Holder.stl, VP_Sleeve_Spinner.stl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]
2024-10-24 PenController sensor abstraction
2024-10-25 Fix sensor syntax
2024-10-28 Add note on screw types
2024-11-06 Move ArduinoInterface and related class files into dedicated folder
2024-11-06 Fix main.py unresolved import and typo
    [main.py]
